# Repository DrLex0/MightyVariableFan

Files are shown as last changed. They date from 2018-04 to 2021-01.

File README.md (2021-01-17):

# MightyVariableFan

*Variable fan speed workaround for 3D printers based on the MightyBoard, like the FlashForge Creator Pro*<br>
by Alexander Thomas, aka Dr. Lex<br>
Version 1.1

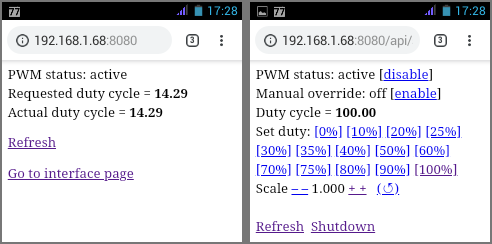
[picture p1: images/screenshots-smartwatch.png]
Screenshots
<br>
[Screenshots of web UI on a smartwatch (view larger image) 🔎](images/screenshots-smartwatch.png)

## What is it?

This adds *full variable print cooling fan speed* capability to 3D printers based on the MightyBoard design like the FlashForge Creator Pro, by means of a kind of *modem connection* between the printer and a Raspberry Pi.

To make this work, you need some minimal understanding of how to use Linux on a Raspberry Pi and at least basic electronics skills. Being able to solder might not be essential but will make it much easier than trying to find ready-made cables that will fit. While working on the internals of your printer, take the usual precautions for working on delicate electronics: avoid static discharges and short-circuits.

This has so far only been tested with *PrusaSlicer* (formerly Slic3r) and (albeit not thoroughly) *Simplify3D.* Quite likely the post-processing script that generates the beep sequences will at this moment only work with G-code generated by those slicers. Of course the main reason why I have published this on *GitHub* is to make it easy for anyone to modify the code and submit pull requests to make it work with other slicer programs.

I have been using this for a year without problems, hence I have created a 1.0 release. There are some minor problems left and some things I would like to improve upon, but I consider the 1.0 release (and newer) very usable. See the *Current Issues* section at the bottom for caveats.<br>
This has only been tested with prints from the SD card, because I don't print through USB. I don't expect problems with USB prints though.

### Motivation

The MightyBoard has one annoying limitation, being lack of **PWM ability for the cooling fan.** The fan is connected to the ‘EXTRA’ output on the board and this output is only a binary toggle, meaning the fan can only be either at full throttle or off. This makes it impossible to get optimal results with filaments that require a small or moderate amount of cooling, and there are many other reasons why one would want to vary the speed of the fan. Programs like Slic3r offer advanced fan speed control but it is worthless with only a binary toggle. What we need is a way to control the fan speed from within G-code, and preferably there should be a manual override as well. 

It is possible to recompile the Sailfish firmware with a software PWM implementation on the EXTRA output, but it is only a static setting that cannot be changed mid-print and it still only reacts to on/off commands without a speed value. A simple manual hardware PWM controller is probably a better option because it will at least allow to change the PWM at any time, but it remains cumbersome. I have done this for a few months until I got tired of having to babysit every print. I wanted fully automatic fan control from within the X3G file itself.

Recently a pull request has been proposed for Sailfish to make the software PWM respond to speed arguments in the G-code, but this still has problems: the commands are still executed with horribly bad timing and there is no manual override (even if it would be added, manipulating it mid-print via the LCD menu is very kludgy). Also, GPX needs to be patched and recompiled to output X3G files with fan speed values included, and this will only work if you have somehow managed to have your slicer generate G-code that is suitable for Sailfish *and* includes variable fan speeds.

The ideal way to tackle this problem is to completely decouple fan speed handling from the firmware. The printer's job is to print, not to accurately control fans. The printer should send fan speed commands to a separate device that does the actual fan PWM in a smart way. I found no straightforward way to send commands from within a print to an external device however. Most infuriatingly, the MightyBoard has a second UART1 serial interface that was originally intended exactly to send commands to external devices, but this feature was dropped for reasons unknown. At best the UART1 port can now be used as an alternative to the regular USB serial port. The ideal solution would be to restore the ability to send arbitrary serial commands through UART1 but this would require extensive changes to the Sailfish firmware code, introducing new G-code commands that would need to be supported by GPX as well. This was the last thing I wanted to try, so I looked for alternative solutions first and I found one even if it isn't the most straightforward.
From experiments, the **buzzer** has proven to be a reliable one-way communication channel. Not only does it play tones with accurate timings, it also plays them exactly where they occur inside the print code, unlike the M126 and M127 commands that toggle the EXTRA output at a rather unpredictable time before the command is expected to be executed. I did some experiments and the concept of using the buzzer as a communication channel proved very viable. So in a nutshell, I have used the buzzer to set up a *modem connection* to the external fan controller.

### How It Works

1. A **post-processing script** called *pwm_postprocessor.py* on your local computer takes G-code with M106 fan speed commands as input, and outputs the same code with those commands replaced by M300 beep commands. These play very specific sequences of 3 high-pitched blips using 4 fixed frequencies. This allows to encode 64 levels, which is plenty for controlling a fan. This script also manipulates the speeds to optimize them (see ‘advantages’ below), and can shift the speed changes to obtain very accurate timings. For this to work, you need to ensure your slicer program generates G-code that contains fan speed commands.
2. A **Raspberry Pi** mounted inside the printer runs a Python daemon called *beepdetect.py* that continuously listens to audio input from a simple USB sound card. A **microphone** attached to this card is placed directly above the printer's buzzer. The script uses an FFT to detect the specific frequencies of the blips.
3. When beepdetect.py detects a sequence, it performs an HTTP call to a simple Python-based web server that also runs on the Pi, this is the *pwm\_server.py* script based on CherryPy.
4. The pwm\_server reacts to incoming calls that request a speed change, by manipulating PWM output on a GPIO pin of the Pi. This is done through the RPi.GPIO Python module (which only implements software PWM, but this is good enough for controlling a fan at low frequency).
5. The GPIO pin controls a simple **MOSFET** break-out board that switches the 24V of the main printer PSU. The fan is connected to this MOSFET's output.

### Advantages

This approach, crazy as it may seem, has quite a few advantages:
* No irreversible modifications to your printer are needed. Although you may need to construct the cables for the microphone and GPIO, you do not need to solder anything on the printer itself. The only requirements are glueing in some 3D printed mounts for the Pi and MOSFET, re-wiring the fan, and mounting a power supply for the Pi. These can all fit inside the spacious insides of an FFCP.
* You do not need to recompile anything. If you would have attempted to do all this stuff inside a heavily hacked Sailfish build, next to that build itself you would also have needed to hack and rebuild the GPX program and possibly your slicer, because otherwise you would have no way of getting the fan speed arguments in an X3G file.
* Decoupling the PWM controller from the printer's firmware allows to add advanced features without having to modify the printer or recompiling firmware. For instance, the PWM server controller has a *kickstart* feature to allow the fan to start at very low speeds and to more quickly reach intermediate speeds.
* The post-processing script can optimize fan speeds and timings. It can ensure the fan will have spun up at the right time, and it can gradually ramp up fan speed between the first layers and higher ones. The latter is very important with most cooling duct designs because at lower layers the cooling may otherwise be excessive due to air being forced in between the platform and the extruders, as well as the material cooling faster due to heat being absorbed by the build platform.
* Timing of fan speed changes can be very accurate, down to the level of one second. This allows to cool only sharp overhangs or bridges without risk of compromising layer adhesion elsewhere in the print.
* If your Pi is connected to a WiFi network, the fan PWM server can be reached through any portable device like your smartphone, and you can monitor and manipulate fan speed at any time without having to fiddle with the printer's LCD menu.
* The PWM server offers temporary or permanent manual override of fan behavior, useful for experimenting or in case you notice you have misconfigured the cooling for a print that would be a pity to abort. A scale factor can be applied to all incoming requests or the fan can be forced to a fixed speed.
* Fan duty cycles as low as 1% can be used even from standstill, thanks to the kickstart.
* If you already have installed a Raspberry Pi in your printer to have a camera feed or control other parts of the printer, you only need to install a USB sound card with microphone, an extra MOSFET, and some wires. (See the PAQ below though.)
* The EXTRA output on your printer becomes available for something else, should you find a use for it.
* Due to the modular design, if someone finds a less crazy way of making the printer communicate with the Pi, only the beepdetect and pwm_postprocessor scripts need to be updated.

### Disadvantages

* There is only one obvious disadvantage: the printer will be making some extra noises as if R2D2 is trying to subtly get your attention. These blips are very short though, and are played at frequencies the buzzer cannot play loud anyway. Thanks to these two design choices, the blips don't really stand out above the usual printer noises.
* A less likely problem is that if your printer is placed next to a pen with pigs that can squeal *extremely* loud at the exact same frequencies as the blips, detection might fail. Please don't combine 3D printing with pigs. More realistic sources of disturbances are nearby machines that make loud hissing noises, or a loud music system very near to the printer. In my setup however, I couldn't even trigger any false responses with the detector in debug mode without making unreasonably loud noises.

If you would suffer from one or both of these problems, they can be reduced or eliminated in several ways. The first way is to print a sealed adapter for attaching the microphone to the buzzer instead of a half-open one. This both attenuates the blips to a nearly inaudible level and reduces influence of external noises.

If you're not afraid of soldering on your printer's main board, you can omit the microphone and make a direct electrical connection between the buzzer contacts (marked ‘BUZZ BUZZ’) and the USB sound card. You should make the connection through a decoupling capacitor and possibly add a resistor divider to attenuate the signal if necessary. This eliminates the outside noise problem completely. Moreover, you can unsolder the buzzer as well if you want to mute it entirely. This ReadMe won't explain how to do all these things: I assume that if you are prepared to solder on your printer's main board, you also have sufficient knowledge how to make this kind of connection correctly.

## PAQ (Possibly Asked Questions)

### Is this really reliable? It can't be!

Yes it is. I have been using it for more than a year now and despite the few glitches mentioned in the ‘current issues’, it works incredibly well.

### Can I run something else on the same Raspberry Pi?

It depends. If the other process consumes a lot of CPU or I/O load, then it risks interfering with the real-time operation of the beep detection. So far someone has reported trying to run this system on the same Pi as Octoprint, and this *failed* because the beep detector couldn't reach the required performance. There was no obvious cause (the octoprint process did not cause an excessive load), but it was a pre-made custom Octoprint Raspbian image which might have contained modifications that interfere with the USB sound card. In other words, your mileage may vary. Safest is to use a dedicated Raspberry Pi for the fan system, they are cheap anyway…

## Installing

### Step 1: gather the required hardware

You need:
* A **Raspberry Pi** that has sufficient oomph to run the beep detector, and also WiFi (not strictly essential, but recommended). I am not sure whether a Pi 2 suffices, but a 3B certainly does. These things are cheap anyway so if you already have an old Pi inside your printer, this might be a good time to upgrade it. You don't need a huge microSD card, 16GB is sufficient.
* A small **5V power supply** for your Pi. Ideally, it should be small enough to fit inside your printer. I used a simple off-the shelf supply ([this one](https://www.conrad.be/p/raspberry-pi-netvoeding-sp-5c-zwart-raspberry-pi-3-b-1462834) to be exact) that I could tuck under a bundle of wires inside the printer. I connected it to the mains contacts of the printer's PSU so the Pi is toggled together with the rest of the printer. If you have a choice between multiple supplies that fit, pick the one with the most flexible cable and the most compact microUSB plug. This is where you'll have to be a bit creative with parts you can find in local stores. You could take apart a USB power supply to more easily connect it to the mains, or you could plug the supply into half an extension cord like I did. Whatever you do, do not create dubious and dangerous constructions that expose mains voltage.
* A **USB sound card.** It will be much easier if it is as small as possible. I recommend to buy one of those extremely cheap ‘3D sound’ sticks with yellow and green 3.5mm jack. These are rather crappy but very compact, well supported in Linux, and for the purpose of this application they are good enough. The plastic case of these cards is unnecessarily large; to make it much easier to fit inside your printer you can print [this custom case](https://www.thingiverse.com/thing:2822474) if it fits your model of sound card (if not, modifying the 3D model should be easy).
* A tiny **microphone** that can be mounted very close (within 10 mm) to the buzzer. I recommend to build your own microphone with a standard electret capsule (9.7mm diameter), a bit of shielded cable, and a 3.5mm plug. This can be mounted perfectly onto the buzzer with a 3D printed part.
* A **24V MOSFET** break-out board. There is a very common one for the IRF520, which is very easy to mount inside the printer with yet another printed part.
* A **cable** to connect the GPIO pins on the Pi to the MOSFET. It is best to solder your own using low-profile or angled plugs because space may be tight depending on where you will mount the Pi.
* A **fan** that supports PWM. If your FFCP came with the ‘squirrel cage’ fan on the left of the carriage, you should be fine. If you don't have a fan yet, it would be a good idea to buy that exact same fan as FlashForge uses, which in my printer is a *Ruiapple DB5015HB24.* If you want to buy another type of fan, you should ensure it can be driven with a PWM signal, which is often *not* the case. Safest is to obtain a 4-wire fan (typically used for PC coolers) that has a separate PWM input, in that case you don't even need the MOSFET. The only problem is that you may have a hard time finding such a fan that works on 24 V, most will require 12 V. You can of course avoid this problem by installing an extra 12 V power supply or step-down converter.

### Step 2: prepare the Raspberry Pi

The following assumes you are running the *Raspbian Stretch* or newer operating system on your Pi. Most likely you are, unless you installed it before July 2017. To verify, check whether the file */etc/debian_version* exists on the Pi and starts with at least *9.*<br>
(If you are running something different for a specific reason, chances are you're knowledgeable enough to adapt the installation procedure to your own needs.)

Installation is relatively simple. The required skills are opening a console or terminal on the Pi and inside it, navigating directories and executing commands. If you've attached a monitor and you are inside the desktop environment, you can launch the ‘Terminal’ program. If the Pi has a network connection and you enabled SSH (e.g. using raspi-config), you can also open an SSH connection from another computer. Tutorials about how to do these things should be easy to find.

On the Pi, download and unzip this project's files, or clone the repository with the `git` command. You only need the contents of the *pi_files* folder but simply downloading everything is easier. You can do this in any way and put the files anywhere you want, but you need to know where they are on the filesystem. Most practical is to put them directly in the home folder of the ‘pi’ user (*/home/pi*).

Upgrade the software on your Pi to the latest versions, especially if it was installed long ago and never updated since. You can do this in several ways, for instance use *Update* in `raspi-config`, or: `sudo apt-get update; sudo apt-get upgrade`. This can take a while if you haven't updated in a while. It is recommended to reboot afterwards.

Now make sure the USB audio device is plugged into the Pi. The next step is to run an installer script that puts all files in place. In your terminal or SSH console, go to the *pi_files* folder using the `cd` command and enter these commands:
```
chmod 755 install.sh
sudo ./install.sh
```

By default the PWM server will run on TCP port 8081. If you want to change this because something else is already running on that port, pass the desired port number as argument to the install command (e.g.: `sudo ./install.sh 8082`). The port number must be higher than 1023 because the server does not run with root privileges.

If this script stops with an ‘ERROR’ message and you cannot figure out how to fix it, you can contact me directly or file an issue on GitHub. If it says *“Everything ready, now starting services,”* then you're good to go.

Before mounting the Pi in your printer, you should also configure everything else to your likings, for instance the WiFi connection, SSH access with public key, hostname, … You should also disable everything you don't need, like the graphical X environment unless you really need it for an attached display. Anything that could produce an unpredictable burst of activity should be disabled to avoid interference with the beep detector.<br>
If you are really adamant on getting the best possible performance, you could install a real-time kernel. However, this seems overkill from my experiences so far (also, it won't help if you're simply attempting to run more than the Pi can handle).<br>
How to do those things is outside the scope of this guide. There is plenty of community support available for the Raspberry Pi!

Originally I planned to add some kind of display with buttons or maybe a touchscreen, to be able to view and manipulate the status of the PWM controller. However, the only good display I found was more expensive than the Pi itself and I realized that a smartphone or even a smartwatch also makes a fine wireless touch display, so I didn't bother.

### Step 3: create the required parts

You need two **cables:** one for the microphone, and one for the MOSFET. The microphone cable will have a 3.5 mm stereo plug on one side, and be directly connected to the electret capsule at the other end (unless you want to add some kind of plug, your choice). The MOSFET cable simply needs two header sockets. At one end, it should be a socket with 2 contacts, to be connected to GPIO pins 12 and 14 on the Pi. If you're using the IRF520 break-out board, at the other end the cable needs a 3-contact socket with the middle one left open. GPIO pin 12 on the Pi needs to be connected to the ‘SIG’ pin on this board, and GPIO pin 14 to its ‘GND’ pin; ignore the VCC pin.

If you're going to install the Pi and MOSFET in the same places as I did (see the ‘mount’ section below), the cable going to the microphone must be 31 cm long (3.5mm jack included), and the cable going to the MOSFET should be about 35 cm. If you already mounted the Pi elsewhere, you will have to figure out how long the cables need to be and how to route them. Important: use either some kind of shielded cable for the microphone connection, or a twisted-pair cable. Don't just use any two-wire cable because it will most likely act as an antenna for noise. For the GPIO connection the cable is less crucial, but a twisted pair cable is still preferred.

If you use a standard electret capsule as microphone, solder the ground/shield connection (the long sleeve on the 3.5 mm plug) to the negative pole of the microphone (which connects to the outside of the capsule), and the other wire to any of the two ‘live’ contacts of a 3.5 mm stereo jack plug. It doesn't matter which one: on the simple ‘3D sound’ cards both contacts are the same anyway. Do not short one of those contacts to ground, just leave it open.

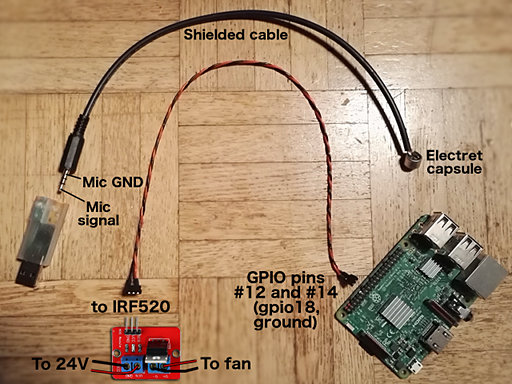
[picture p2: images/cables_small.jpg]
Cables
<br>
[Cables (view larger image) 🔎](images/cables.jpg)

Next, you need some **3D printed parts** to mount the components. They can be found in the *models* folder. The recommended layer height for all these is 0.2 mm.

* **A mount for the Raspberry Pi.** If you mount it in the position I recommend below, the `RaspberryPiMount` brackets should be optimal. These were designed for a model 3B but should in theory fit any model. You need two 2.2×6.5 mm self-tapping screws to secure the Pi after sliding it into the rear notches. To ensure the underside of the mount is flat and easy to glue, rub it against a sheet of sandpaper with the Pi mounted. The regular bracket raises the Pi **23 mm** from the bottom, which is a bit of a compromise between offering room for wires plugged into the GPIO pins, and avoiding that the microUSB power cable needs to bend too much due to the cramped space. Use this one if the power cable is not very flexible. You will need low-profile GPIO header plugs or angled plugs, the regular tall plugs won't fit. The `19mm` brackets raise the Pi only **19 mm,** which offers more room for GPIO plugs but will require a small microUSB power plug with a flexible cable. Of course you can also design your own brackets or use any other mount that works.<br>
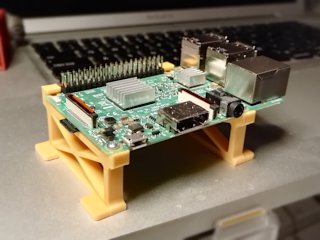
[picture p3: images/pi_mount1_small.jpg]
Pi mount
  [🔎](images/pi_mount1.jpg)
* **A mount for the MOSFET.** If you use the ubiquitous IRF520 break-out board, the `IRF520-MosfetMount.stl` model should be suitable, it uses the same 2.2 mm self-tapping screws as the mount for the Pi.<br>
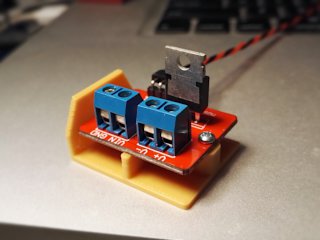
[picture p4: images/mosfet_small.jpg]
MOSFET
  [🔎](images/mosfet.jpg)
* **An adaptor to mount the microphone** onto the buzzer of the printer's main board. Two models are provided that fit a standard 9.7 mm electret capsule. As described above, if you want to keep the buzzer sounds as they are, use the half-open model `BUZZ-Electret-mount.stl`. The closed model `BUZZ-electret-mount-sealed.stl` can be used to mute most of the sound of the buzzer in case you don't want to hear the beep sequences and don't care that other beeps like the start-up song will be muted as well. It is strongly recommended to print this adaptor in a *flexible* filament to dampen vibrations and make mounting easier. If you are using a different model of microphone, again you will need to figure out something on your own, but make sure the mic is as close as possible to the buzzer and there is minimal contact with anything that vibrates.<br>
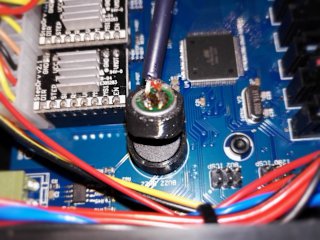
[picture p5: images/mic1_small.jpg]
Microphone 1
  [🔎](images/mic1.jpg)

### Step 4: sanity check

Before mounting everything, it is a good idea to do a sanity check of the whole system outside the printer. The nice thing about the typical IRF520 board is that it has an LED that will light up if there is a signal on its GPIO input, even if nothing else is connected. Plug the sound card into the Pi and connect the MOSFET to the GPIO. The GPIO pins #12 (GPIO 18) and #14 (ground) must be connected respectively to the ‘SIG’ and ‘GND’ contacts of the MOSFET board ([here](https://www.raspberrypi.org/documentation/usage/gpio/) is documentation about the GPIO pins).

Next, power up the Pi. After a few seconds you should see the LED on the IRF520 board light up momentarily. If in a browser you enter the Pi's IP address on port 8081 or the custom port number you configured (e.g. `http://192.168.12.34:8081/`), you should see the interface of the PWM server and be able to change the intensity of the LED by choosing different duty cycles.

Next, plug in the microphone, log into the Pi through SSH and run:
```
sudo stoppwmservices
arecord -V mono -D micsnoop -f S16_LE -r 44100 test.wav
```
Say something into the microphone and stop the arecord process with ctrl-C. If you then copy the resulting test.wav file to your computer and play it, you should hear what you have recorded. If not, check the connections and alsamixer settings for the USB sound card (see the ‘calibrating’ section). Also verify that the `hw:1,0` ALSA device is actually the microphone, if not then update the ‘pcm’ value in `/etc/asound.conf`. If the recording is OK but has an awful lot of low-frequency noise, then the cable going to the microphone is poorly shielded and picking up WiFi interference. You might get away with this, but it is better to use a proper shielded cable.

### Step 5: mount and connect the parts

If you haven't yet mounted a Raspberry Pi in your printer and you do not want to optimize its position for attaching a RPi camera with its rather short flatcable, I recommend to mount it in the front side of the bottom chamber next to the power supply, as shown in the overview image. This position ensures the WiFi antenna will have good signal reception without being near any other circuit of the printer, moreover it offers easy routing of the microphone, MOSFET and USB power cables. Of course, feel free to mount the Pi anywhere else, but as always you're on your own then.

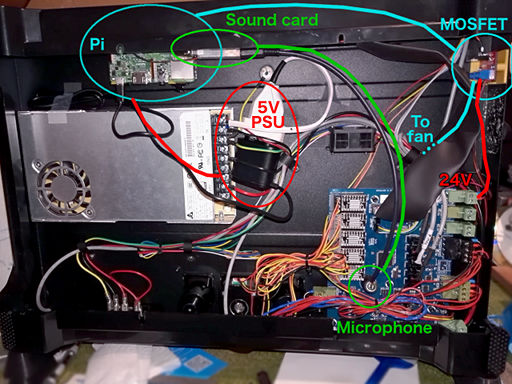
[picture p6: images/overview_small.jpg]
Overview
<br>
[Overview (view larger image) 🔎](images/overview.jpg)

If you are using my 3D printed Pi mount, you can stick it to the printer's housing with epoxy glue. You should first verify there is enough room for cables and plugs *before* fixing the position of the mount. By all means glue the mount with the Pi inside it and the sound card and cables plugged into the Pi, otherwise there is no guarantee it will fit afterwards. This is also why you shouldn't use cyanoacrylate (super glue): it won't give you time to correct the position if you got it wrong.

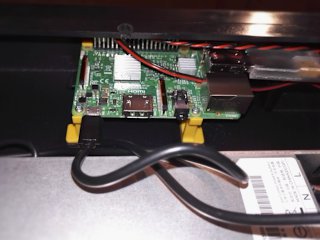
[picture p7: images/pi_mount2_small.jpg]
Pi mounted
[🔎](images/pi_mount2.jpg)

How you can mount the 5V power supply, will depend on its shape. In the overview photo you can see that my supply was small enough to simply tuck under a bundle of wires. I connected it to the mains voltage terminals of the main supply through part of an extension cable. This ensured a safe connection, as opposed to my first stupid idea of trying to wrap something around the plugs and covering them with shrink-wrap tubing, which I quickly abandoned when trying it in practice. If your idea seems vaguely dangerous, it most likely is and must not be attempted. In case of doubt, either ask assistance from someone more experienced with electronics or keep the power supply outside your printer and plug it into a regular power socket.

Installing the microphone is straightforward: push it into the mount, and the mount onto the buzzer. Insert the 3.5 mm plug into the input jack of the sound card (yellow on ‘3D sound’). Ensure the plug is perfectly clean to avoid getting random bad contacts. Try to avoid that the microphone cable touches the motherboard fan (unless you disabled this fan because apparently it is not really necessary).

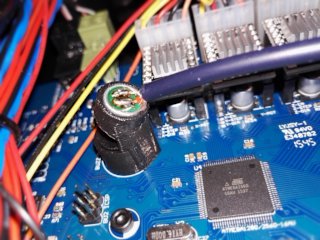
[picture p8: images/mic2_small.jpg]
Microphone 2
[🔎](images/mic2.jpg)

Now you can mount the MOSFET (unless you're using a 4-wire fan, then you don't need this). Connect all the wires before fixing its mount in place. Disconnect the fan wires from the EXTRA output socket, and connect them to the V+ (red) and V- (black) terminals of the board. Next, you need to get 24V from somewhere. You can either use a long wire directly to one of the unused 24V terminals of the power supply, or you can use a short wire to the ‘FAN’ output on the corner of the board, which is hard-wired to the 24V as well. Make sure to get the polarity right! GND is negative (usually black wire), VIN is positive (usually red wire). Don't forget to connect the GPIO as described at the start of this section. Once everything is connected, find a good place to glue the mount.

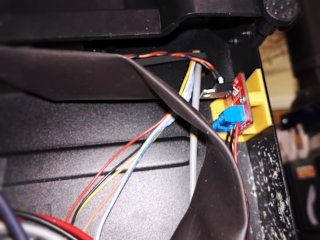
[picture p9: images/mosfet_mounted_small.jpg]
MOSFET
[🔎](images/mosfet_mounted.jpg)

If you are using your own 4-wire fan instead, omit the MOSFET and simply connect the PWM output pin of the Pi to the fan's PWM wire, and the power wires to GND and V+. If you're using a 12 V power supply, make sure to connect its ground to the ground of the Pi. These fans usually require a PWM frequency of 25 kHz, hence you will need to add this line to the defaults file: `PWM_FREQ = 25000` (see below for how to do this).

When you power on the printer and Pi, after a few seconds you should see the fan spinning up for a few seconds. If this doesn't happen, it could mean the pwm_server.py script was not properly installed or one of the electrical connections is incorrect.

### Step 6: calibrating

When everything has been installed and set up, the last step is to calibrate the beep detector. This step is **crucial** because if the system is not properly configured, fan speed changes may be missed and prints may get cooled at too high or low speed or not at all.

Calibration mode performs a few tests regardless of what it detects and it also outputs statistics about any signal frequencies it has detected. To begin with, we'll do a sanity check to see if the script achieves the required **performance.** Before entering calibration mode, you must stop the regular detector: run `sudo stoppwmservices`. Then run `beepdetect.py -c`. It will probably start by spewing many warnings which you may ignore as long as in the end you see “Calibration mode” appear.

For the performance check, just leave it alone for at least 30 seconds and then press *ctrl-C* to stop it. Look for “PERFORMANCE CHECK” in the output. If it reads “Looks OK” then continue with the steps below. If it says “too slow” then try again but let it run for at least a minute. If it keeps on reporting “too slow” or even “WAY TOO SLOW,” then you're in trouble because the script cannot achieve the required speed. Check again whether you really have a recent Raspberry Pi (3B or newer). If you do, maybe something else running on it is consuming way too many CPU or I/O resources. If you cannot shut down any other processes, you only option is to install a separate Pi to run the PWM system.

If the performance test checks out, the next important thing is to configure the **input gain** of the USB sound card. Open a second terminal connection to the Pi and run `alsamixer`. Inside the alsamixer UI, press *F6* to select the USB sound card (most likely the last one in the list). Next, press *F5* to show all controls (or F4 for capture, but this doesn't always work). The cheap ‘3D sound’ card only has one ‘capture’ control, select it with left/right arrow keys. If it doesn't read ‘CAPTURE’ in red below the indicator bar, press the space bar. The gain is adjusted with arrow up and down keys. Start out by cranking up the gain to the maximum (100).

With alsamixer still open, again run `beepdetect.py -c` in the other console. Now load the *BeepCalibration.x3g* file on your printer and print it. It consists of two parts: the first plays a set of beep sequences that uniformly cover all signals, the second part plays noises. With the ALSA gain at maximum, you should see `“WARNING: Clipping detected”` appear. Your goal now is to reduce the gain in alsamixer to the highest level where clipping no longer occurs during the normal beep sequences. Gradually lower the mic gain (down arrow) and play the file again from the start, and repeat until you no longer see any clipping warnings during the first part while the normal beep sequences are playing. It is OK and actually desirable that there is still clipping during the noise in the second part of the BeepCalibration file. If you do not see the clipping warning even with gain at maximum, there may be something wrong with your microphone or audio setup.

Once you have tuned the gain just below the point where no more clipping occurs, exit alsamixer (Esc key) and run `sudo alsactl store`. This will preserve the setting across reboots. Stop the beepdetect process by pressing ctrl-C. If your setup is similar to mine and you tweak the gain like this, then it is likely the system will just work at this point, but it is always a good idea to **verify** this by performing the following steps.

Once the microphone gain has been set, you can fine-tune some **other parameters.** The beep detector and PWM server both read their **configuration** from a *defaults* file located at */etc/default/mightyvariablefan*. If any of the parameters need to be changed, modify this file using your favorite text editor. (Do not edit the scripts themselves, this will make it difficult to upgrade them.)<br>
Restart calibration mode with `beepdetect -c` and play the first part of the BeepCalibration file again, then press ctrl-C and look at the output. It will contain the following sections:
* **PERFORMANCE CHECK:** this has already been covered above. The chunks-per-second measure is only accurate if the script has been running for at least a few dozen seconds, but you may ignore the error about calibration time being too short if you previously verified that performance is OK.
* **SCALING FACTORS:** the responses to the different signal frequencies need different scale factors because the buzzer does not play each tone at the same amplitude and the microphone does not have a flat frequency response either. The script will show a set of suggested scale factors ‘`SIG_SCALEs`’. Physics dictate these values should normally be an increasing series. If this is not the case for the suggested values, something fishy may be going on. If it looks OK but the values deviate considerably from the current `SIG_SCALEs`, then you should copy the suggested lines to the *defaults* file. (These values may vary across different runs. For maximum accuracy, run calibration multiple times and take averages across runs.)
* **suggested sensitivity:** this is the threshold at which a tone is considered a potentially valid signal, obviously this is an extremely important parameter. If the suggested sensitivity deviates a lot from the current value, ensure there is a line in the *defaults* file that specifies “`SENSITIVITY = …`” with the suggested value.
* **DETECTION BINS:** this verifies whether the script is listening to the optimal FFT bins, which are configured as `SIG_BIN1` to `SIG_BIN4`. Again, due to the frequency response of your particular buzzer and microphone, it is possible that the theoretically optimal bins do not match the actual bins.
  * If the script says: *“Bin … looks good”* four times, then you're good to go.
  * If one or more lines state *“Bin x appears to be better than bin y,”* then it may be a good idea to add the suggested `SIG_BIN` definitions to the *defaults* file. You should then re-run calibration, but if the better bin indices keep on drifting away from their theoretically ideal positions, something is definitely wrong.

Once you're done, either reboot the Pi or run `sudo startpwmservices` to resume normal operation. You could then re-play the BeepCalibration file and check in */var/log/beepdetect.log* whether the series of sequences `012, 301, 230, 123` is detected three times (and the fan changes speed accordingly). This is not a fool-proof verification but at least a good indication that the system works correctly.

### Optional step: install custom firmware

This step is not strictly necessary depending on what Sailfish firmware version you're currently running. Recent releases of the firmware have an annoying feature that interferes with the MightyVariableFan system: they always play a song each time all heaters have reached their target temperature, even during prints. If this tune starts right in the middle of one of the beep sequences, that particular fan speed change will not be executed, which could be disastrous in worst-case situations.

If you are running an older version that does not play these tunes during prints and you do not plan to update it, then you don't need to do anything. Otherwise if your version does play the tunes, or you want to have all the latest improvements to Sailfish, then you only really have one option: [install the custom firmware build from my Sailfish branch](https://github.com/DrLex0/Sailfish-MightyBoardFirmware/releases/tag/20180505) (available for all other MightyBoard-based printers supported by Sailfish as well). This build allows to prevent the heaters tune from being played during printing, by means of an extra toggle in the LCD menu at `Utilities` → `General Settings` → `Heaters Sound`. Set this to `OFF` after installing this firmware.

I have created a [pull request](https://github.com/jetty840/Sailfish-MightyBoardFirmware/pull/201) on the main Sailfish repository that adds this same heater tune toggle, but it is unlikely this will ever make it into official builds, especially because development on this main branch seems to have stagnated. Even if it does, there is no guarantee that FlashForge (or your particular manufacturer) will distribute such a build anytime soon. For this reason you should flash my custom build. It also includes other recent improvements that probably are not yet incorporated in official builds available from printer manufacturers, for that reason alone it could be worth upgrading to it.

## Using

Once you have the setup running, all that is left to be done is to end up with print files that contain beep sequences instead of the old M126 and M127 commands. To do this, your regular G-code must be run through the *pwm_postprocessor.py* script. This script has so far only been tested with G-code produced by *PrusaSlicer* and *Simplify3D.* It might work with other slicers, but most likely the script will require a few modifications. (If you can make those modifications yourself, a pull request to merge the improvements would be welcome. If not, you can also send me a few G-code files and I can see how to make the script work for them.)

The problem is that some slicer programs are aware of the limited fan capability of MightyBoard-based printers, hence they only use fan on/off commands without any speed information if you ask them to output Sailfish-compatible G-code. There are two possible situations:
1. Your slicer outputs M126 commands without an ‘`S`’ argument. This is the case with PrusaSlicer or Slic3r. In this case, the solution is to change your printer profile to output G-code for *RepRap* instead, which contains M106 and M107 commands with speed arguments.
2. Your slicer does output M126 commands with an `S` argument. This is the case for Simplify3D. In this case, you must invoke the postprocessing script with an extra `-S` argument to tell it to accept the M126 commands.

The `-S` option can also be used to convert files that contain M126 and M127 commands without speed arguments. In that case the speed for M126 commands will be assumed to be maximum.

You need *Python 3.5* or newer on the machine where you'll be running the postprocessor script. Inside the script, you may need to make one important change: ensure `END_MARKER` is set to a line that indicates the print has ended. If you are using your own snippet of end G-code, just ensure it starts with a unique comment line and copy that exact line into the script. Of course you can avoid having to modify the script by just inserting the default `END_MARKER` line into your own end G-code.

There are other adjustments you can make, these can also be passed as command-line arguments:

* `RAMP_UP_ZMAX` is the zone above the build plate within which fan speeds will be gradually scaled starting from a scale factor `RAMP_UP_SCALE0` at *Z* = 0, to 100% at *Z* = `RAMP_UP_ZMAX`. The reason why this is recommended, is because airflow from the cooling duct bounces off the bed at the lower layers, and it is also being forced in between the bed and the extruders. This causes more cooling than expected, and it can also cause extruder temperature to drop if the fan suddenly activates at high speed. The optimal values of these parameters will differ depending on what kind of cooling duct design you use. You will have to experiment. (Note: this feature works better than the similar one in Cura because it uses a fixed Z height instead of counting layers that might have different heights.)
* `LEAD_TIME` is the number of seconds by which beep sequences should be moved forward in time. A sequence takes about 0.7 seconds to be played and detected, and the time needed to spin up the fan must also be considered, hence a value around 1 second should be reasonable. In my case 1.2 seconds seems optimal. Mind that this is done on a best-effort basis. The time will not always be exact because the script doesn't consider acceleration, and granularity depends on duration of print moves. If the last move before an original M106 command takes more than twice `LEAD_TIME`, the script will not be able to anticipate the beep sequence. The script can split up long moves to obtain a good lead time, this is the `--allow_split` option which is off by default. It is possible that enabling this option can cause visible artefacts, so there is a bit of a trade-off between cooling performance and surface quality.
* `FEED_FACTOR` and `FEED_LIMIT_Z` are values specific to the FlashForge Creator Pro and it is unlikely you need to change them, only do so if you know what you are doing.

Once the script has been configured, you can either manually run it on every G-code file you want to print (run with `-h` for more information), or you can somehow automate it inside your workflow. How you can do the latter, depends on your slicing program. In case you use PrusaSlicer with [my (DrLex) configuration](https://www.dr-lex.be/software/ffcp-slic3r-profiles.html), the latest version of the `make_fcp_x3g` script can invoke the PWM post-processing script as well.

**Note:** even if you reconfigure your slicer to output RepRap-flavor G-code, the GPX program to convert G-code into X3G must still be configured to output code for your specific printer model (e.g. `-m fcp` for the FlashForge Creator Pro)!

### Web interface
During a print you can observe the current PWM duty cycle and manipulate it if you wish, by opening the PWM web server interface on a computer, tablet or smartphone. The default address is `http://your.RPi.address:8081/`. (Port number may be different if you changed it.) The interface is currently still very crude but should be self-explanatory. Next to setting some fixed PWM preset values, you can also increase or decrease a **scale factor** in 5% steps. This factor will be applied to every incoming PWM value, which can be useful if you notice you have configured too low or high fan speeds for a print.

The interface also allows to *shut down the Pi cleanly.* This is not terribly important but recommended if the Pi's power supply is behind the same switch as the printer's. It is better to perform a clean shutdown than simply pulling the power. Wait at least 15 seconds for the Pi to shut down before disconnecting the mains.

If you want to make the interface accessible from an outside network where it is undesirable that anyone can manipulate the fan controller, you can set up simple **authentication** with a username and password. The basic status page can always be viewed without logging in but if both a username and password have been configured, login credentials will be asked when trying to access the interface page. To do this, edit the file */etc/default/mightyvariablefan* and add these lines (obviously use a nontrivial username and password):
```
PWM_USER = "someName"
PWM_PASS = "somePassword"
```
Reboot the Pi to apply these changes. There is a ‘logout’ link but this only works in certain browsers (like Chrome) due to limitations of the digest-based authentication method. In other browsers the only way to log out is to quit and reopen the browser. Mind that the server uses plain HTTP which means login credentials could theoretically be sniffed from network traffic. If you want to prevent this, I would advise to not rely on plain port forwarding to make this application available over the internet but instead place it behind a HTTPS reverse proxy like [Nginx](https://www.nginx.com/) (you can also use this to add extra protection like rate limiting).

### Tools and tweaks
In the Tools folder there are files `PWMFanOff.x3g` and `PWMFanMax.x3g` that play the sequences for disabling the fan and setting it to 100%. These are useful for several things:
* if you abort a print, the fan will remain at its last speed. You can use the ‘off’ file to stop the fan if you don't have direct access to the PWM web interface.
* as a quick routine test of the system after booting up your printer. This is especially recommended if you're about to do a print where correct cooling is crucial. So far I've had one occasion where the microphone didn't pick up any sound after I had taken the system apart and reassembled it (most likely a bad contact with the 3.5 mm plug, it was fixed after I had cleaned the plug and reinserted it).

Last but not least, if you previously neglected fan speed values in your slicer profiles (as you should have), now is the time to go through them again and try to enter sensible values. Optimal values will differ between each filament and also depend on what kind of extruder, nozzle, and cooling duct you are using. Be prepared to experiment and tweak! Also be prepared to be amazed at how much of a quality improvement proper cooling can provide.

This system is compatible with version 0.7 or newer of my [dualstrusion post-processing script](https://www.dr-lex.be/software/print3d-dualstrusion.html) to improve dual extrusion prints on the FFCP.

## Technical details

(This is only for interested nerds. If you just want to use the system, skip this section.)

Look in the source code comments for most of the particularities of how the system works.

The reason why we're recording from an ALSA *dsnoop* slave device is that this eliminates the issue of clock skew between the sound card and the host. When recording directly from the raw device, eventually enough drift between the clocks will build up such that a buffer overflow (if the sound card runs faster) or underrun (slower) occurs. This will lead respectively to either omission of a chunk of data, or repeating the same chunk twice. Both are obviously bad for a detection system which relies on short beep sounds. The dsnoop device does continuous resampling instead of abrupt corrections. The resampling quality is probably not audiophile-grade, but the FFT couldn't care less as long as there is a continuous flow of samples without gaps or repetitions.

The IRF520 MOSFET is theoretically capable of drawing up to 9 A of current. However, with the low gate voltage provided by the Pi, the maximum current will be much lower. For switching the cooling fan it is perfectly adequate but keep this in mind should you would want to switch heavier loads.

## Current Issues

There still is a very tiny risk that a detection may be missed (judging from my tests, the risk is perhaps 1 in 1000). I plan to redesign the detection logic to be more robust. I believe though that the printer may very rarely botch up playback of an M300 command as well. To avoid that a missed detection at an unfortunate moment could ruin a print, I plan to modify the post-processing script to repeat sequences at important locations.

If you would be running your own custom build based on the very latest Sailfish master branch, you will run into a problem caused by the ‘hammerfix’ commits by *dbavatar* from around July 2016: M300 commands (to play beeps) cause a significant pause in the print, and the sequences are played with sloppier timings that will cause beepdetect.py to miss them. I have made a [pull request](https://github.com/jetty840/Sailfish-MightyBoardFirmware/pull/202) that nearly eliminates the pauses by improving SD card reading efficiency. The sloppy beep playback is still a problem but I plan to rewrite the detection algorithm in beepdetect.py anyway such that it is more robust. For those who do want to try the hammer fix, ask and I'll make a build that includes it. You should first try [my other custom build](https://github.com/DrLex0/Sailfish-MightyBoardFirmware/releases/tag/20180505) however, perhaps the included SD card reading improvement will already provide the performance boost you're looking for.

Next to the tiny risk of a missed detection, there is also a considerably higher risk of tunes played by the printer to cause a false detection. This means such tune can turn on the fan or change its speed to something unpredictable. When using my custom firmware build that disables the heater tunes during printing, this is not much of a problem: each print should start with a ‘fan off’ command anyway, and there is no harm if the fan is inadvertently left spinning by the tune that signals the end of the print (if you have one in your end G-code). With other builds it can be very problematic however, which is why I highly recommend to use [my custom firmware build](https://github.com/DrLex0/Sailfish-MightyBoardFirmware/releases/tag/20180505). Anyway, this problem would also be solved by a more robust detection strategy.

### Disclaimer

This software, instruction guide, and 3D models, are provided as-is with no guarantees of any kind. Performing this modification to your printer is entirely at your own risk. The author(s) claim no responsibility for any possible damage or harm caused by attempting to follow these instructions or using any of the provided resources.

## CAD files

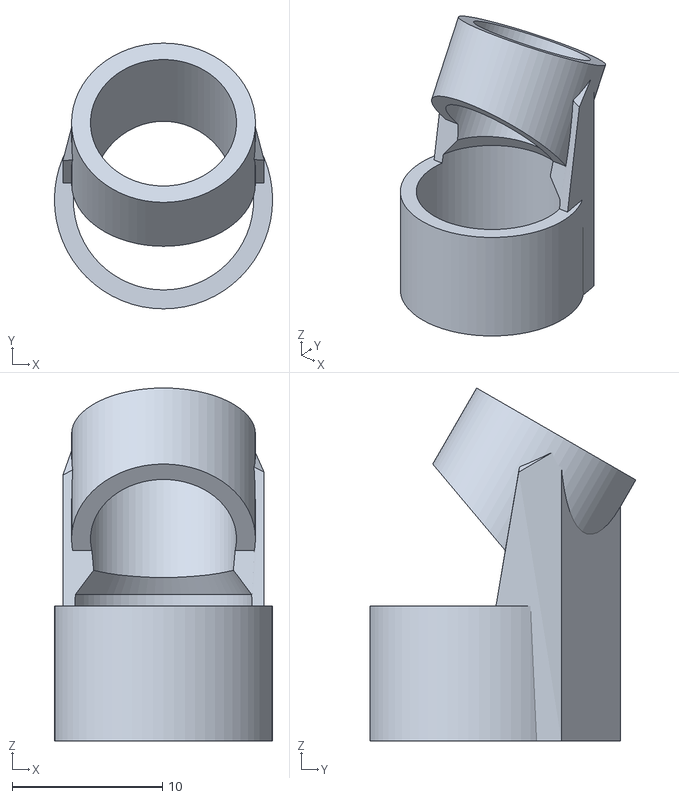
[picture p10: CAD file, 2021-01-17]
models/BUZZ-Electret-mount.stl
14.5 x 17.7 x 23.5

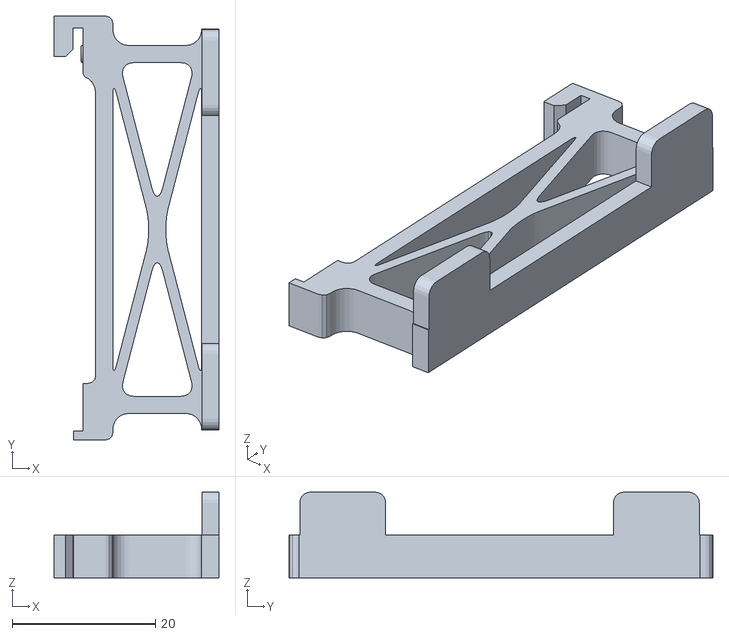
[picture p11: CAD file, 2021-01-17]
models/RaspberryPiMount-19mm-R.stl
23.0 x 59.2 x 12.0

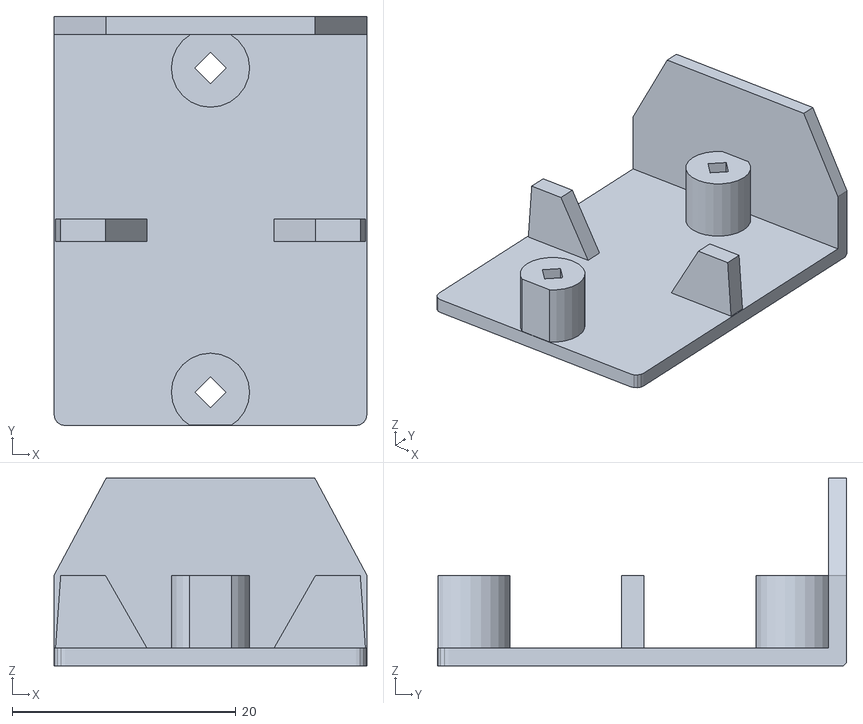
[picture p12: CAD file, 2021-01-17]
models/IRF520-MosfetMount.stl
28.0 x 36.6 x 16.8

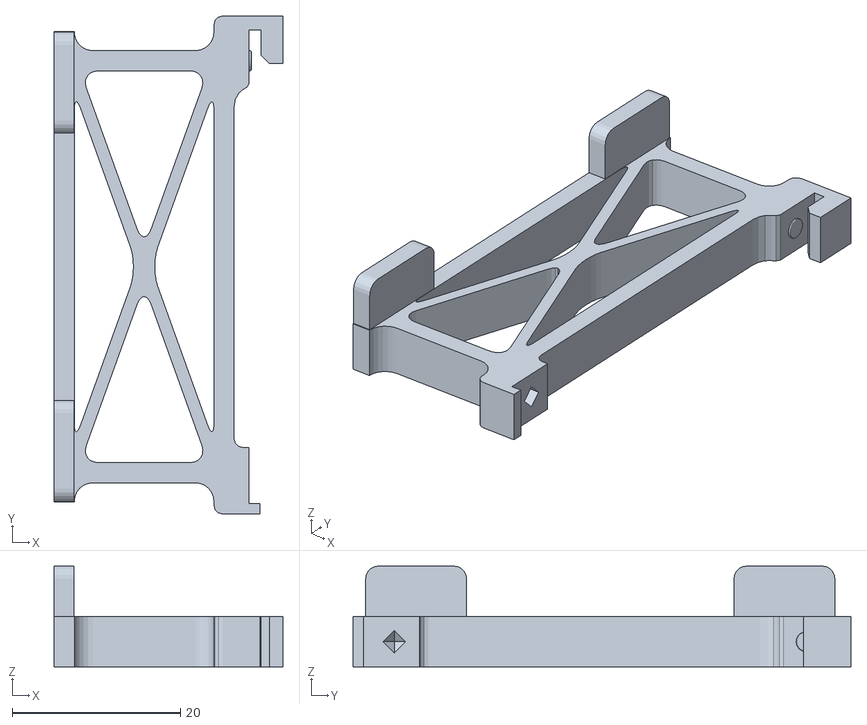
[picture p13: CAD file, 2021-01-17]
models/RaspberryPiMount-L.stl
27.2 x 59.2 x 12.0

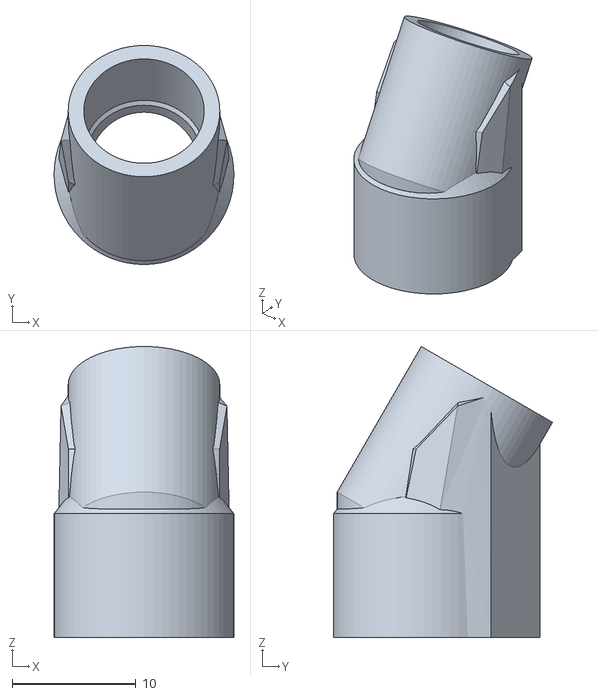
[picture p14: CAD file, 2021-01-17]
models/BUZZ-electret-mount-sealed.stl
14.5 x 17.7 x 23.5

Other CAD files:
models/RaspberryPiMount-R.stl
models/RaspberryPiMount-19mm-L.stl

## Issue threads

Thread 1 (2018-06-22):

Investigate possibility of communicating with the Pi through UART1

DrLex0, 2018-06-22:
One of the motivations for using the buzzer as a communication channel was that it doesn't require installing a custom firmware. However, due to the annoying heaters tune played by recent Sailfish builds, a custom firmware build is needed anyway to remove the risk of this tune messing up beep sequences. The pull request to toggle the tune might some day be merged into Sailfish, but it could take forever before this ends up in firmware that the average Joe can easily install.

Hence if (for the time being) a special Sailfish build needs to be flashed anyway, the possibility should be investigated whether an extra X3G command could be added that can send short strings to the second serial output (UART1) of the MightyBoard. This would provide a more reliable communication (and silent) channel to the Raspberry Pi, and open up the possibility to control many other external devices from within a print.

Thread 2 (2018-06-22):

Implement ‘paranoid mode’ in pwm_postprocessor

DrLex0, 2018-06-22:
It seems impossible to eliminate the risk of missed detections completely. Occasionally a detection still fails due to one of the beeps not being recognized. It is unclear why, maybe the printer just botches up an M300 command or maybe there still is an occasional glitch in the audio stream. The risk of this happening seems to be around the level of 1/1000 which makes it nearly impossible to debug.

Still, the risk remains that such failure will happen right at the moment the last fan speed change for a long while is supposed to be performed. If this is missed, the fan could keep blowing at much too high or low speed and ruin the print.

A workaround is to repeat a sequence after a few seconds, if no new sequence follows within reasonable time (say 10 seconds). The risk that two consecutive sequences fail should be extremely low.

The streamed data flow in pwm_postprocessor makes this a bit tricky to implement. The simplest way is probably to make two passes over the G-code, keeping track of when and where sequences were inserted during the first pass and then inserting duplicates in the second pass.

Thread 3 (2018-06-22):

Make detections in beepdetect.py more robust

DrLex0, 2018-06-22:
Currently the detection algorithm is biased towards positive signals. Any series of three signal frequencies with acceptable timings is treated as a positive. There is only some awareness of negative indicators like harmonic detection. The result is that some of the tunes can still trigger a false positive. This is not really a problem when using the Sailfish build with the heater tune toggle option, but it is annoying.

Another problem is that playback of M300 commands will likely become less accurate in future releases of Sailfish. This means the detection parameters will need to be made more lenient which again increases the risk of false positives.

To both reduce the risk of false positives while allowing more sloppy timings, I propose to update the detection routine to evaluate groups of 3 possible signals as a whole instead of sequentially.
The false positives I have seen, all have a whole bunch of ignored simultaneous signals. The motivation for this was that a sharp bang on the printer housing must not cause a detection to be aborted, but a sharp bang will only cause 1 or maybe 2 FFT frames with multiple signals, not 10 like I often see in a false detection. So if a candidate sequence has more than 2 simultaneous signals, discard it.
Similar for timings: if the timing of one beep and one pause is somewhat too long but the other timings were perfect, the printer was probably slowed down while playing an actual sequence and it should be accepted. If all timings are suspicious, then it should be discarded.

This can be implemented as a penalty system where each simultaneous signal case adds a score, an each timing flaw adds another score. If the score exceeds a threshold, discard.

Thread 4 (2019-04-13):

Simplify3D Postprocessing

joeynuggetz, 2019-04-13:
Just followed this guide and put everything together and all is working and all calibrations are good. Only problem is I use S3D and not Slic3r and was wondering if you could provide a way to post-process the GCODE that is output from S3D. Tried feeding some S3D gcode into the phython script and it complained that M126/M127 commands are being used. Found some in the start gcode (also some in your Slic3r start/stop snippets). Can you provide some guidance please? I really need to use S3D due to the processes.

DrLex0, 2019-04-13:
You need to use the alternate ‘MVF’ start snippet with this system. If you then configure S3D to output G-code for a RepRap printer instead of Sailfish, it might work. At the least this should get you to a point where the script breaks due to my assumptions of how Slic3r formats G-code. If that's the case then it should only be a matter of making the G-code parsing more universal.

joeynuggetz, 2019-04-14:
I think I figured out the problem. S3D appends the top of the gcode file with comments of all the slicer settings which includes the start/end gcode and perhaps the END_MARKER that the script is looking for- ";- - - Custom finish printing G-code for FlashForge Creator Pro - - -" Is it that simple?

 I removed all the comments at the start of the file and re-ran the processor and it worked. Haven't printed with it yet but the M300 commands are in there.  With the gcode as is straight from S3D the script will give a "WARNING: M126 and/or M127 command(s) were found inside the body of the G-code. Most likely, your fan will not work for this print. Are you sure your slicer is outputting G-code with M106 commands (e.g. RepRap G-code flavor)?"

DrLex0, 2019-04-14:
Can you provide an example of a non-processed G-code file as S3D produces?
The detection of neither the M126/127 code nor the end line marker should trip on anything that is prepended with the ‘;’ comment character.

joeynuggetz, 2019-04-14:
Sure, here you go
[S3D_unprocessed.zip](https://github.com/DrLex0/MightyVariableFan/files/3077391/S3D_unprocessed.zip)

DrLex0, 2019-04-14:
It seems S3D does append S (speed) arguments to M126 commands even though this is useless for a non-modified FFCP. This means I could add an ‘s3d’ mode to the script that simply accepts M126 commands with S arguments, then you wouldn't need to do anything special except invoke the script with this option. The rest of the G-code seems compatible with the script.

I am slightly confused though if the current script works for you with this particular file if you strip the comment lines from it, because it contains M126 and M127 commands in the code itself. The script should still complain even with all comment lines removed and no M300 sequences should be inserted except maybe one at the end of the file. If everything works as intended, you should see a bunch of M300 sequences around the first layer changes with steadily increasing effective speeds, until `RAMP_UP_ZMAX` has been reached.

joeynuggetz, 2019-04-14:
Thanks for looking. I haven’t tried stripping the comments from this code but I followed the same process yesterday and stripped the comments and the script doesn’t complain when I post process. If you could have a version of the script that is S3D frilendly that would be cool and I would be happy to test. I will try and run the scripts with the comments disabled. I did it yesterday and like you said I saw m300 command right at the 2nd layer where I had the fan set to kick in.

BTW if anyone hasn’t said so recently let me say that you are a freaking genius. Having the ability to PWM a fan on the flashforge is epic. I really enjoyed doing this little modification. You’re the man. Wish I had half your brain power. :-)

joeynuggetz, 2019-04-14:
Tried to strip the comments in the start of the gcode file I shared with you and this time it still errors out so you are correct that simply removing the comments would still cause the script to fail.  So what specifically do I need to tweak to get it to work?

DrLex0, 2019-04-14:
I have updated the script. There was indeed an issue with the ‘`@body`’ marker inside the parameter dump being wrongly detected as the start of the actual print. This is now fixed so you no longer need to strip the comments, and you also don't need to set the printer type to RepRap anymore.

joeynuggetz, 2019-04-14:
Awesome!. Just tested with the -S option and it worked. I see the M300 commands in the output now. Nice job.
I'm trying to adopt your startup and ending gcode snippets that I'm sure you spent a lot of time on to S3D. There's one variable that Slic3r uses **G1 Z[first_layer_height] F1500; move to first layer height** that I can't find an equivalent to in S3D. I found the variables for extruder and bed heating and I'm sorta stuck on this one.

DrLex0, 2019-04-14:
I cannot find this either and I doubt it is available at all. However, it isn't crucial to use the actual first layer height in the start code. You can hard-code any sensible value, I would recommend 0.25 since that's usually the first layer height I use and it works well for the priming extrusion.

DrLex0, 2019-06-02:
I'm going to close this assuming S3D support is now good enough, if there's anything else, just open a new issue :)

Closed 2019-06-02.

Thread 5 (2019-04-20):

Consider acceleration to estimate timings

DrLex0, 2019-04-20:
Add an option to take acceleration into account when calculating the duration of print moves. This will make the timing of the fan speed changes more accurate. Currently the timings can be off by quite a bit if there are many small zig-zag moves right before a fan speed change, because these are slowed down considerably by accelerated moves.
Ideally the splitting of print moves should also take acceleration into account, but I reckon this will require a lot of effort for only a marginal improvement, the simple linear split should be good enough.

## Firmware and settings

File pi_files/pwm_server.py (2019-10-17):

#!/usr/bin/env python3
"""
A basic server that allows to control the PWM output pin through HTTP requests, also offering
  a crude web interface to manually control the PWM.
The server can be switched to manual override mode, which requires every control request to
  have a 'manual=1' argument.

Alexander Thomas a.k.a. DrLex, https://www.dr-lex.be/
Released under Creative Commons Attribution 4.0 International license.
"""

import argparse
import os
import random
import string
import subprocess
import sys
import time

import cherrypy
from cherrypy.lib import auth_digest
import RPi.GPIO as rpi_gpio


#### Defaults ####
# The preferred way to override these is to define them in the defaults file at DEFAULTS_PATH
# (see below). Anything defined in that file has priority over the values defined below,
# but command-line arguments have the highest priority.

PWM_SERVER_PORT = 8081
STATIC_CONTENT_DIR = "/home/pi/pwm_server"

# Optional authentication for the server. Empty username or password disables authentication.
# The root of the server is always accessible but only allows viewing basic status.
# If authentication is enabled, access to the /api path requires login.
PWM_USER = ''
PWM_PASS = ''

# The GPIO pin to use.
# The software PWM in RPi.GPIO seems decent enough for controlling a fan because minor jitter
# doesn't matter. However if it does prove to be troublesome, a solution that uses hardware PWM
# will be needed instead. For this reason it is recommended to use GPIO pin 12 so you wouldn't
# need to open up things and re-plug cables if this change is made.
# (Another good reason for pin 12 is that it is practical, it is next to GND pin 14.)
PWM_PIN = 12
# My fan doesn't like high PWM frequencies. 200Hz works very well and helps with low duty cycles.
# You may be able to reduce noise by carefully choosing this value.
PWM_FREQ = 200
# Lowest allowed duty cycle (%), meaning the lowest duty cycle where the fan won't stall. This
# value will override any nonzero duty cycle below it.
# Believe it or not, my fan still runs at 1% DC.
PWM_MIN_DC = 1.0

# PWM kickstart parameters. Kickstart always works at 100% duty cycle, only the duration of the
#   'kick' varies.
# The time to kick when we start from zero, it must be enough to bring the fan above stall speed.
PWM_KICK_LAUNCH = 0.20
# The duration of a kick is calculated as the difference in duty cycles (percentages) multiplied
# by this factor. This should be tuned such that the fan just doesn't overshoot (or only slightly
# overshoots) the target speed.
PWM_KICK_FACTOR = 0.01

# In case you're running this on something else than a Pi
MACHINE_NAME = "Raspberry Pi"

#### End of defaults section ####


#### Configuration section for fixed values ####

# Path to the defaults configuration file
DEFAULTS_PATH = "/etc/default/mightyvariablefan"

# Path to the lock file of beepdetect.py, will be used to show a warning if it isn't running.
DETECTOR_LOCK_FILE = "/run/lock/beepdetect.lock"

#### End of configuration section ####


def html(title, body):
    """Wrap the body HTML in a mobile-friendly HTML5 page with given title and CSS file
    'style.css' from the static content directory."""
    return """<!DOCTYPE html>
<HTML>
<HEAD>
<TITLE>{}</TITLE>
<META name="viewport" content="width=device-width, initial-scale=1.0">
<LINK rel="stylesheet" href="/style.css" type="text/css">
</HEAD>
<BODY>
{}
</BODY>
</HTML>
""".format(title, body)


class PWMController:
    """Allows to control a GPIO pin on the Raspberry Pi with PWM output, with support for
    'kickstarting' the output to help with starting at low target speeds, and faster
    transitioning to higher speeds."""

    def __init__(self, config):
        """Create a new PWMController.
        @config must be an ArgumentParser arguments object."""
        self.pwm_min_dc = config.minimum_dc
        self.kick_launch = config.kick_launch
        self.kick_factor = config.kick_factor
        self.kickstart = bool(config.kick_launch or config.kick_factor)
        rpi_gpio.setmode(rpi_gpio.BOARD)
        rpi_gpio.setup(config.pin, rpi_gpio.OUT)
        self.pwm_out = rpi_gpio.PWM(config.pin, config.frequency)
        self.active = False
        self.duty_in = 0.0  # The unscaled last requested duty cycle
        self.duty = 0.0  # Actual set duty cycle
        self.scale = 1.0

        self.pwm_out.start(self.duty)  # clear any leftover state
        self.pwm_out.stop()

    def __del__(self):
        self.shutdown()

    def scale_duty(self, duty):
        """Return effective duty cycle according to scale and minimum duty cycle."""
        eff_duty = duty * self.scale
        if eff_duty > 100.0:
            return 100.0
        if eff_duty and eff_duty < self.pwm_min_dc:
            return self.pwm_min_dc
        return eff_duty

    def set_duty(self, duty, kick_override=None):
        """Sets the duty cycle of the output.
        The actual duty cycle will be determined by scale and minimum duty cycle.
        Global kickstart behavior can be overridden by passing a boolean in @kick_override."""
        current_duty = self.duty
        self.duty_in = duty
        self.duty = self.scale_duty(duty) if self.active else 0.0
        if self.duty:
            do_kickstart = kick_override if kick_override is not None else self.kickstart
            # Don't bother with kickstart if the target DC is near 1 anyway
            if do_kickstart and self.duty > current_duty and self.duty < 95.0:
                kick_duration = (self.duty - current_duty) * self.kick_factor
                if current_duty == 0 and kick_duration < self.kick_launch:
                    kick_duration = self.kick_launch
                if not current_duty:
                    self.pwm_out.start(100)
                else:
                    self.pwm_out.ChangeDutyCycle(100)
                # Ideally this should be handled asynchronously, but due to the short times
                # I deem it too much hassle for what it's worth.
                time.sleep(kick_duration)
            if not current_duty:
                self.pwm_out.start(self.duty)
            else:
                self.pwm_out.ChangeDutyCycle(self.duty)
        else:
            self.pwm_out.stop()

    def set_scale(self, scale):
        """Change the scale factor and update the PWM output accordingly."""
        self.scale = scale
        self.set_duty(self.duty_in)

    def activate(self, active=True):
        """Sets the enabled state of the PWM output. If disabled, the output remains off
        regardless of what other commands are given. If re-enabled, the PWM output is
        restored according to the last requested parameters."""
        self.active = active
        self.set_duty(self.duty_in)

    def ramp_up_test(self):
        """Sweeps the PWM from zero to max over 3 seconds, then returns to previous level."""
        if not self.duty:
            self.pwm_out.start(0.0)
        for i in range(0, 101, 5):
            self.pwm_out.ChangeDutyCycle(i)
            time.sleep(0.15)
        self.set_duty(self.duty_in)

    def shutdown(self):
        """To be invoked when about to stop the server."""
        if self.pwm_out is not None:
            self.pwm_out.stop()
            self.pwm_out = None
            rpi_gpio.cleanup()


class GpioDisplay:  # pylint: disable=too-few-public-methods
    """Basic page that shows current PWM state and offers access to the API page."""

    def __init__(self, pwm):
        self.pwm = pwm

    @cherrypy.expose
    def index(self):
        """Display the main (and only) page."""
        active = "active" if self.pwm.active else "<span class='warn'>inactive</span>"
        duty_raw = "Requested duty cycle = <b>{:.2f}</b>".format(self.pwm.duty_in)
        duty = "Actual duty cycle = <b>{:.2f}</b>".format(self.pwm.duty)
        detector_warning = ""
        if not os.path.exists(DETECTOR_LOCK_FILE):
            detector_warning = "<br><span class='warn'>Warning: beepdetect is not running!</span>"
        links = "<p><a href='/'>Refresh</a></p>\n<p><a href='/api/'>Go to interface page</a></p>"

        cherrypy.response.headers["Cache-Control"] = "max-age=0, max-stale=0"
        return html(
            "PWM Server",
            "PWM status: {}<br>{}<br>{}{}{}".format(
                active, duty_raw, duty, detector_warning, links))


class GpioAPI:
    """Handles HTTP requests to control the PWM output."""

    def __init__(self, pwm, config):
        """Create a new server.
        @config must be an ArgumentParser arguments object."""
        self.pwm = pwm
        self.override = False
        self.machine_name = config.name
        self.has_auth = bool(config.user and config.password)
        self.shutdown_token = None

    def shutdown_machine(self):
        """Initiate a shutdown of the machine this script runs on."""
        # Prevent the beep detector from reviving the PWM (even though that would mean you're
        # shutting down the Pi while the printer is still working).
        self.override = True
        # If I don't do this, RPi.GPIO will hang and postpone the shutdown.
        self.pwm.shutdown()
        # Instead of invoking shutdown directly, do it via a script that forks and then invokes
        # shutdown after a few seconds, so we still have time to return a response and do not
        # need to try something awkward to make CherryPy commit seppuku.
        subprocess.Popen(["/usr/local/bin/shutdownpi"], cwd="/")
        # I tried invoking cherrypy.engine.exit() here. Bad idea: somehow it delays the stopping
        # of the server compared to just waiting for the SIGHUP or SIGKILL.
        return html(
            "Shutdown initiated",
            ("<p>The {} will now shut down.</p>".format(self.machine_name) +
             "<p>Wait at least 15 seconds before pulling the power!</p>" +
             "<p><a href='/'>Main page (in case you power on again)</a></p>"))

    def server_status(self, basic=None):
        """This is the main page that will be returned upon every normal successful request.
        If @basic evaluates to True, any extras will be disabled and the response will be minimal.
        This should be be a simple page that can be used to control all basic functions of the
        server from a smallish touch display.
        TODO: create a much nicer UI that always stretches itself across small screens."""
        cherrypy.response.headers["Cache-Control"] = "max-age=0, max-stale=0"

        active = "active" if self.pwm.active else "<span class='warn'>inactive</span>"
        scale = self.pwm.scale
        if basic:
            scaled = ", scale {:.2f}".format(scale) if scale != 1.0 else ""
            return html(
                "PWM Server",
                "PWM status: {}, duty cycle = <b>{:.2f}</b>{}".format(
                    active, self.pwm.duty_in, scaled))

        if self.pwm.active:
            pwm_toggle = "<a href='disable?manual=1'>disable</a>"
        else:
            pwm_toggle = "<a href='enable?manual=1'>enable</a>"

        override = "<span class='warn'>ON</span>" if self.override else "off"
        if self.override:
            manual_toggle = "<a href='man_override?enable=0'>disable</a>"
        else:
            manual_toggle = "<a href='man_override?enable=1'>enable</a>"

        detector_warning = ""
        if not os.path.exists(DETECTOR_LOCK_FILE):
            detector_warning = "<br><span class='warn'>Warning: beepdetect is not running!</span>"

        # TODO: increment/decrement buttons next to presets, or replace presets with a slider
        pwm_presets = ["<a href='setduty?d={d}&manual=1'>[{d}%]</a>".format(d=duty)
                       for duty in [0, 10, 20, 25, 30, 35, 40, 50, 60, 70, 75, 80, 90, 100]]
        scaler = "1.000" if scale == 1.0 else "<b>{:.3f}</b>".format(scale)
        scaler = "Scale <b><a href='scale?factor=0.95238'>– –</a></b> {} "\
                 "<b><a href='scale?factor=1.05'>+ +</a></b>&nbsp;&nbsp; "\
                 "<a href='scale?reset=1'>(↺)</a><br>".format(scaler)
        effective_duty = self.pwm.scale_duty(self.pwm.duty_in)
        scaled = " ({:.2f} scaled)".format(effective_duty) if scale != 1.0 else ""

        shutdown = "<br><a href='/api/'>Refresh</a>&nbsp; <a href='shutdown'>Shutdown</a>"
        logout = "<br><a href='logout'>Logout</a>" if self.has_auth else ""

        return html(
            "PWM Server on {}".format(self.machine_name),
            ("PWM status: {} [{}]<br>".format(active, pwm_toggle) +
             "Manual override: {} [{}]<br>".format(override, manual_toggle) +
             "Duty cycle = <b>{:.2f}</b>{}<br>".format(self.pwm.duty_in, scaled) +
             "Set duty: {}<br>{}{}{}{}".format(" ".join(pwm_presets), scaler,
                                               detector_warning, shutdown, logout)))

    @staticmethod
    def needs_override():
        """Returns the page to be shown if a request was ignored due to manual override."""
        return html(
            "Manual override in effect",
            "Ignoring this request because the server is in manual override mode, and \
the request lacks the 'manual' parameter.<br><a href='/api/'>Back</a>")

    @cherrypy.expose
    def index(self, basic=None):
        """The main page."""
        return self.server_status(basic)

    @cherrypy.expose
    #pylint: disable=invalid-name
    def setduty(self, d, manual=None, basic=None):
        """Sets the PWM duty cycle.
        @d must be a number between 0.0 and 100.0, where 0 is off and 100 is full power.
        @manual means this request has manual override authority.
        If @basic, only a minimal status page is returned."""
        try:
            duty_value = float(d)
            if duty_value < 0 or duty_value > 100:
                raise ValueError("value out of range")
        except ValueError as err:
            # 422 was originally intended for WebDAV, but it has become a more general response
            # for 'invalid parameter value'.
            raise cherrypy.HTTPError(
                422,
                ("Invalid value '{}' for d parameter: ".format(d) +
                 "it must be a number between 0.0 and 100.0 ({})".format(err)))

        if self.override and not manual:
            return GpioAPI.needs_override()

        self.pwm.set_duty(duty_value)
        return self.server_status(basic)

    @cherrypy.expose
    def scale(self, factor=1.05, reset=None):
        """Multiplies the current scale multiplier by the given @factor with 0 < @factor < 100.
        Both the current duty cycle as well as any future incoming ones (manual or not)
        will be scaled by the resulting global multiplier.
        Because this is only meant for manual override, there is no 'manual' or
        'basic' argument.
        If @reset evaluates to True, @factor is ignored and the multiplier is reset to 1.0."""
        try:
            scale_value = float(factor)
            if scale_value <= 0 or scale_value >= 100:
                raise ValueError("value out of range")
        except ValueError as err:
            raise cherrypy.HTTPError(
                422,
                ("Invalid value '{}' for factor parameter: ".format(factor) +
                 "it must be a number larger than 0.0 and less than 100.0 ({})".format(err)))
        if reset:
            new_scale = 1.0
        else:
            new_scale = self.pwm.scale * scale_value
            if round(new_scale, 3) == 1.0:
                new_scale = 1.0
        self.pwm.set_scale(new_scale)
        return self.server_status()

    @cherrypy.expose
    def enable(self, manual=None, basic=None):
        """Enables the PWM output, resuming any previously set duty cycle."""
        if self.override and not manual:
            return GpioAPI.needs_override()
        self.pwm.activate()
        return self.server_status(basic)

    @cherrypy.expose
    def disable(self, manual=None, basic=None):
        """Disables the PWM output."""
        if self.override and not manual:
            return GpioAPI.needs_override()
        self.pwm.activate(False)
        return self.server_status(basic)

    @cherrypy.expose
    def man_override(self, enable):
        """Enables or disables the manual override mode."""
        # Why not just 'override' as path? Because there is already a member variable with
        # that name and this causes CherryPy to not recognize it as a path.
        self.override = True if enable and enable != "0" else False
        return self.server_status()

    @cherrypy.expose
    # pylint: disable=no-self-use
    def logout(self):
        """Trigger logout. There is no real way to log out from Digest auth, but some
        recent browsers will invalidate the auth when receiving a 401 response."""
        raise cherrypy.HTTPError(401, "LOGOUT")

    @staticmethod
    # pylint: disable=unused-argument
    def logged_out(status, message, traceback, version):
        """Handler for '401 Unauthorized' HTTPError."""
        if message == "LOGOUT":
            # HTML passed through message will be escaped, so we must generate it here.
            message = "<p>Depending on your browser, you might have been logged out. \
If not, you will need to quit and reopen your browser to force a logout.</p>\
<p><a href='/'>Return to main view</a></p>"
        return html(status, message)

    @cherrypy.expose
    def shutdown(self, token=None):
        """This is provided to allow shutting down the Pi cleanly from a web interface, which
        is better than just pulling the power. To minimize the risk of accidentally shutting
        down, e.g. because a browser tries to prefetch a page or reloads it from history, a
        token is generated when loading this URL, and only if the URL is reinvoked with this
        token, will the shutdown be initiated."""
        if self.shutdown_token == -1:
            return html(
                "Shutting down",
                ("<p>Shutdown already initiated!</p>" +
                 "<p><a href='/'>Main page (in case you power on again)</a></p>"))
        if token:
            if token == self.shutdown_token:
                self.shutdown_token = -1
                return self.shutdown_machine()
            return html(
                "Shutdown request ignored",
                ("<p>Invalid shutdown token. Your browser may be trying to reload an old page.</p>"
                 + "<p><a href='/api/'>Return to API page</a></p>"))

        self.shutdown_token = "".join(
            random.choice(string.ascii_lowercase + string.digits) for _ in range(16))
        return html(
            "Confirm shutdown",
            ("<p>Really shutdown the {}?</p>".format(self.machine_name) +
             "<p><a href='shutdown?token={}'>Yes</a>&nbsp; ".format(self.shutdown_token) +
             "<a href='/api/' class='big'>No!</a></p>"))


def read_defaults():
    """If there is a defaults file, override allowed values if the file specifies them.
    Format of the file is Python-style variable definitions, comments starting with #."""
    # Explicitly test on limited set of keys to disallow overriding arbitrary things
    overridable_defaults = [
        'PWM_SERVER_PORT', 'STATIC_CONTENT_DIR', 'PWM_USER', 'PWM_PASS', 'PWM_PIN',
        'PWM_FREQ', 'PWM_MIN_DC', 'PWM_KICK_LAUNCH', 'PWM_KICK_FACTOR', 'MACHINE_NAME'
    ]
    if os.path.isfile(DEFAULTS_PATH):
        line_index = 0
        with open(DEFAULTS_PATH, 'r') as def_file:
            while True:
                line = def_file.readline()
                line_index += 1
                if not line:
                    break
                line = line.split('#', 1)[0].strip()
                try:
                    key, _ = line.split('=', 1)
                except ValueError:
                    continue
                key = key.strip()
                if not key in overridable_defaults:
                    continue
                try:
                    exec("global {}\n{}".format(key, line))
                except Exception as err:
                    print("ERROR: failed to parse line {} in {}: {}".format(
                        line_index, DEFAULTS_PATH, err), file=sys.stderr)
                    sys.exit(3)
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

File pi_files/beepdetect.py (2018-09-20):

#!/usr/bin/env python3
"""
Beep sequence detector script for variable fan speed on a MightyBoard-based 3D printer.
Make sure this is started at about the same time the PWM control server has fully started.

Why and How:
The MightyBoard totally lacks a way of sending serial commands from within G-code / X3G to an
  external device. The only thing it can do, is toggle a device through the EXTRA output.
  Therefore I came up with this somewhat crazy solution of using beeps from the buzzer to send
  digital data to an external device like a fan PWM controller, a bit like a modem.
The workflow is to configure your slicer to output G-code for a printer that supports variable
  fan speed commands. Then, use a post-processing script to convert those commands into
  sequences of 3 beeps played with the M300 command, using 4 specific frequencies and specific
  timings (M300 S0 inserts a pause). Each sequence represents a 6-bit number which is then
  mapped to a 64-level PWM value.
This Python script, running on e.g. a Raspberry Pi, continuously analyses an FFT of audio input,
  and sends a command to a PWM controller daemon whenever it detects a sequence of the signal
  frequencies with the right timing. (The script can be easily adapted to listen to sequences of
  4 beeps, which allows to send a whole whopping byte of information per sequence!)
This works fine with a microphone if it is placed very close to the buzzer, using a mount made
  from a flexible material to minimize noises from the stepper motors being transferred to the
  mic. A more robust alternative (that allows to remove the buzzer as well if it drives you
  crazy), is to solder a direct electrical connection between the buzzer contacts and your audio
  input (through a decoupling capacitor). This makes the system impervious against noises like
  pigs squealing exactly at the high signal frequencies, which obviously happens all the time
  while 3D printing.
This script only consumes between 5 and 7% of CPU on a Raspberry Pi 3, so it can run many other
  things at the same time. However, this should be run at a low 'nice' value to ensure it gets
  priority over other processes.

Alexander Thomas a.k.a. DrLex, https://www.dr-lex.be/
Released under Creative Commons Attribution 4.0 International license.
"""

# TODO: revise detection algorithm to allow even sloppier beep playback. If two M300 commands
#   within one sequence were stretched, it should still be deemed OK. To compensate for the extra
#   sloppiness, there should be a more strict test on silence between the beeps. Maybe the
#   continuous tone check should be enabled after all.
# TODO: calibration mode should check whether all the expected sequences could be detected (don't
#   need the same detection algorithm, can use something more crude).


import argparse
import logging
import os
import sys
from collections import deque
from operator import add
from time import sleep, time

import pyaudio
import requests
from requests.auth import HTTPDigestAuth
from requests_futures.sessions import FuturesSession
# pylint: disable=no-name-in-module
from numpy import short, frombuffer, zeros
from scipy import fft


#### Defaults ####
# The preferred way to override these is to define them in the defaults file at DEFAULTS_PATH
# (see below). Anything defined in that file has priority over the values defined below,
# but command-line arguments have the highest priority.

PWM_SERVER_IP = "127.0.0.1"
PWM_SERVER_PORT = 8081

# Optional authentication for the server. Empty username or password disables authentication.
PWM_USER = ''
PWM_PASS = ''

# Maximum seconds for performing a request to the PWM server. Because these requests are offloaded
# to a separate thread, this (plus 1 second) is also the time before the result will be checked
# and errors will be reported.
PWM_REQUEST_TIMEOUT = 4

# Device ID as used by PyAudio. If set to None, the default device will be used. If this is
# the wrong one, invoke this script with -L and use the device ID that corresponds to the
# 'micsnoop' device.
AUDIO_DEVICE = None

# Sensitivity threshold for detecting signals. This is tricky! Too low threshold will lead to
# false detections, down to the point where even a slight echo of a real signal can cause
# problems. Obviously, too high threshold will lead to missed detections.
# Normally, the default should be fine if you configured the sound card as described in the README
# file. If you do want to verify it, run this script in calibration mode (-c option) and 'print'
# the BeepCalibration file. Exit the script (ctrl-C) when the LCD panel tells you to. Amidst the
# console output will be a suggested threshold value.
SENSITIVITY = 20.0

# Indices of the frequency bins that are used for signals. The frequency for bin i is:
#   i*SAMPLING_RATE/NUM_SAMPLES.
SIG_BIN1 = 139
SIG_BIN2 = 151
SIG_BIN3 = 161
SIG_BIN4 = 172

# Scale factors for each bin, applied before thresholding on sensitivity. These may vary between
# microphones and buzzers. When running the calibration procedure exactly as prescribed, you will
# automatically get suggested values to enter here. The scales are not used during calibration,
# which is why the calibration procedure should be run at a lower sensitivity setting.
SIG_SCALE1 = 1.0
SIG_SCALE2 = 1.8
SIG_SCALE3 = 2.9
SIG_SCALE4 = 3.6

#### End of defaults section ####


#### Configuration section for fixed values ####

# Path to the defaults configuration file
DEFAULTS_PATH = "/etc/default/mightyvariablefan"

# Make sure this matches what your sound card can handle. Lower is actually better, because it
# means higher frequency resolution for the same size of FFT.
SAMPLING_RATE = 44100

# Number of samples in the FFT. This must be small enough to be able to detect a single beep, but
# a beep must not span more than 2 windows. The duration over which a single window is calculated,
# is NUM_SAMPLES/SAMPLING_RATE seconds.
# For 44.1k and 1024 samples, this is 23.2ms or 43.07 windows per second.
NUM_SAMPLES = 1024

# Indices of the bins that may contain frequencies produced by the buzzer. Anything outside this
# will be ignored. (Only used if DETECT_CONTINUOUS is enabled)
TONE_BIN_LOWER = 3
TONE_BIN_UPPER = 174

# If True, explicitly reset detection state when detecting a loud continuous tone.
# This is experimental and I do not recommend enabling it. The idea was to provide a barrier zone
#   around the moment the printer plays a song or error tone. However, in retrospect it only
#   really protects against an X3G file playing a song that happens to have signal frequencies in
#   it at the exact right timings, which is exceedingly unlikely. On the other hand, enabling this
#   check means the detector is temporarily deaf every time there is a very loud continuous tone
#   near the printer, e.g. from a loud music player.
DETECT_CONTINUOUS = False
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

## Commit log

2018-03-25 First working version of pwm_postprocessor script. (No lead time implementation yet.)
2018-03-27 Make sequence length configurable; add initial scale for ramp-up and drop RAMP_UP_START (it makes little sense and complicates logic); warn if M126 is found in print body; argparse for beepdetect.py
2018-03-27 Beep detector: allow beeps to be one FFT window longer, because the printer sometimes plays them slightly longer than expected. Also clean up formatting.
2018-03-27 Clean up PWM server code, add command-line arguments, and spit-polish the ugly web interface.
2018-03-28 Raspberry Pi + Python + package names ending in Py or Pi = confusing.
2018-03-30 Avoid repeating the same beep sequence; improve defaults handling; prepare for lead time implementation
    [beepdetect.py]
2018-03-30 Fix broken defaults when using argparse.SUPPRESS
    [beepdetect.py]
2018-04-04 Improve calibration procedure and provide G-code and X3G file.
2018-04-09 Add utility files that play sequences for fan on and off.
2018-04-09 Postprocessing: no lead time for final ‘fan off’ command; fix missing end marker line.
2018-04-11 Prevent launching multiple instances of beepdetect.py, and show a warning in the PWM server UI if it isn't running.
    [beepdetect.py, pwm_server.py]
2018-04-13 Implement splitting of long moves in pwm_postprocessor
2018-04-15 Rewrite a big part of the pwm_postproc.py logic to better handle M106 commands very close to each other (in number of lines but not necessarily in time). Drop useless speed changes like trying to spi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
2018-04-16 Add timings annotation mode to pwm_postprocessor, and clean up config handling.
2018-04-17 Fix speed bookkeeping bug in pwm_postprocessor, and tweak default values.
2018-04-17 Update README: add current issues
2018-04-19 Ensure shutdown works correctly (after long and tedious debugging).
    [pwm_server.py]
2018-04-25 Major refactor of pwm_postprocessor to better filter out pointless short fan speed changes. Also makes it more feasible to impose a maximum number of sequences per time interval (TODO). Add proper lo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
    [beepdetect.py]
2018-04-29 Implement protection against tune buffer overflowing in pwm_postprocessor. This isn't perfect, very nasty sequences of fan commands might still be risky, but a watertight solution would require way m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
2018-04-30 Improve detection reliability: introduce SIG_SCALES, tweak harmonic detection. Also make calibration much more user-friendly.
2018-05-02 Allow selecting a different audio device in beepdetect.py
2018-05-03 Improve detection reliability: record through an ALSA dsnoop slave device to get continuous resampling; tweak buffers and reduce sleep time between polling the buffers. This seems to have eliminated 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
    [beepdetect.py]
2018-05-06 Make pwm_postprocessor.py robust against character set problems
2018-06-19 Ensure compatibility with my dualstrusion postprocessing script by adding time estimates for certain non-print moves. (Not strictly necessary but small effort anyway.)
2018-06-19 … or rather version 0.7
2018-06-22 Reduce the risk of accidentally hitting the ‘yes’ link on the shutdown webpage while actually wanting to hit ‘no’.
2018-06-26 Add some more presets to the PWM server web page. Increment/decrement buttons would of course be much more practical.
2018-06-26 Add retry mechanism in beepdetect.py if PWM server request fails (apparently it is possible to get a ‘Connection aborted’ in very rare occasions).
    [beepdetect.py]
2018-09-04 Make it easier to run the PWM server on a different port number
2018-09-07 Use frombuffer instead of fromstring to obtain audio data. Binary mode of fromstring is deprecated, moreover frombuffer is more efficient because it doesn't copy the data.
    [beepdetect.py]
2018-09-07 Improve instructions for calibration procedure
2018-09-07 Remind to update packages before deploying. Also ensure calibration info appears after ALSA spam.
2018-09-12 Run beepdetect at highest ‘nice’ priority
2018-09-17 Fix: stderr from pwm_server went nowhere
2018-09-18 Add optional authentication to server. Overhaul pwm_server.py to better separate PWM and web server parts.
2019-04-14 Issue #4: add support for Simplify3D.
    Allow M126 commands with S arguments if the -S option is enabled.
    Also assume an M106/M126 command without S argument means ‘max speed’ instead of ‘off’.
2019-04-20 Add instructions for using a 4-wire fan
2019-10-17 Prevent caching.
    Does not help though with the annoying feature of Google Chrome often believing one really prefers seeing an outdated page on mobile devices, instead of waiting slightly longer for the latest page.
    [pwm_server.py]
2021-01-17 Ignore comments and empty lines when looking for `ahead_layer_z`
    PrusaSlicer 2.3.0 now inserts comments between the fan command and `G1 Z`.
2021-01-17 Migrate 3D models from Thingiverse to this repository.
    Not only because Thingiverse is in a state of rot, it's just easier to have everything in the same place.
    [BUZZ-Electret-mount.stl, BUZZ-electret-mount-sealed.stl, IRF520-MosfetMount.stl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]
2021-01-17 Release 1.1
    Changes since 1.0:
    * Simplify3D support
    * Avoid caching in PWM web UI
    * Avoid unnecessary PWM sequence with PrusaSlicer 2.3
    * PWM postprocessing script is slightly faster
    * Include 3D printed parts in repository
